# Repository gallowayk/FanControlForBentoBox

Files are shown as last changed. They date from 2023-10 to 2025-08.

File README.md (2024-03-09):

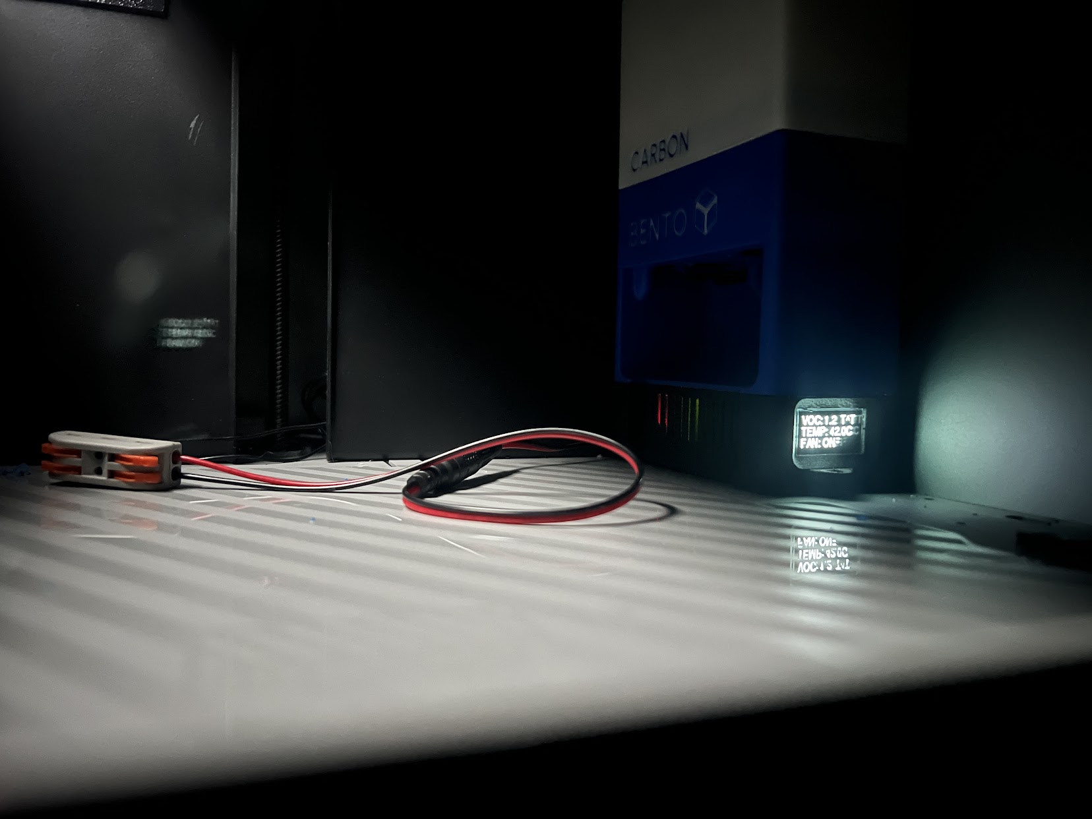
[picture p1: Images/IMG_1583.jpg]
Full Unit in Place


After printing out the Bento Box filtration model, I wanted a means to control the fans so they weren't on 24/7 and only enabled when high VOC content was present. Originally, I was only going to use a bimetal temp switch since the ambient internal temperature of the printer would only rise while printing ABS, PC, Nylon, etc. However, I wanted to take a more sophisticated approach while keeping costs low. 

**Electronics**
- RPi Pico (any variant)
- 3.3V trigger opto-isolated relay https://www.amazon.com/dp/B07XGZSYJV 
- MS1100 gas sensor https://www.amazon.com/dp/B0BF4JDW26
- AHT21 temperature and humidity sensor https://www.amazon.com/HiLetgo-Precision-Temperature-Humidity-2-0-5-5V/dp/B09KGW1G41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
- 128x64px SSD1306 OLED screen https://www.amazon.com/gp/product/B0833PF7ML 
- LM2596S buck converter https://www.amazon.com/gp/product/B07QKHR6PY 
    - The buck converter must be adjusted to +5VDC or +3/3.3VDC

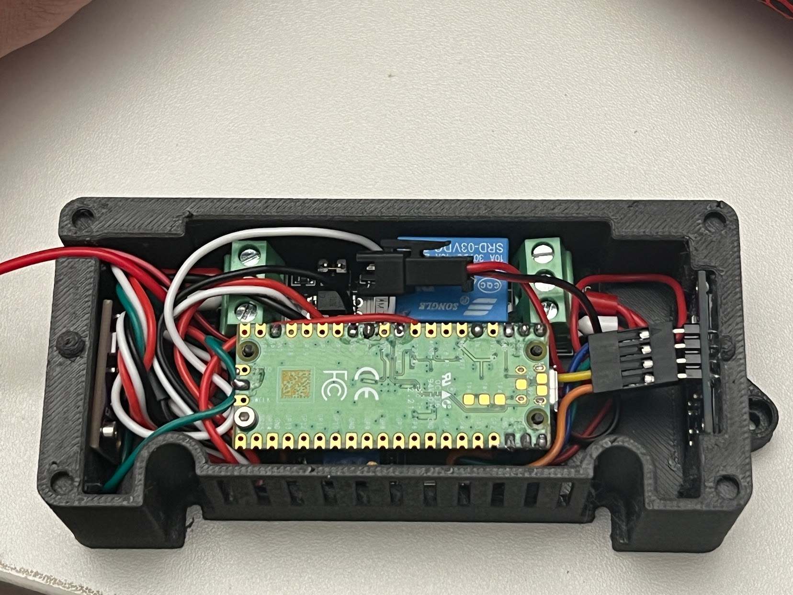
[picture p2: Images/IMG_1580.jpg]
Assembled Electronics box


**Hardware**
- 2x M2x5 or M2x8 self-tapping screw
  - One for VOC sensor
  - One for RPi Pico
- 8x 4x2mm Magnets
- Various jumper wires
- Helps to use male to female jumper wires
- It also helps to have a Dupont connection/terminal kit and crimper; this will allow you to make your own wires of just the right length

**Tools**
- Soldering iron
- TS100 is my go-to due to its rapid heating and cooling
- "Helping hands" for soldering
- Precision tool set
- Ball-end hex keys can be used as well
- Ferrule crimper + ferrules
- Heatshrink

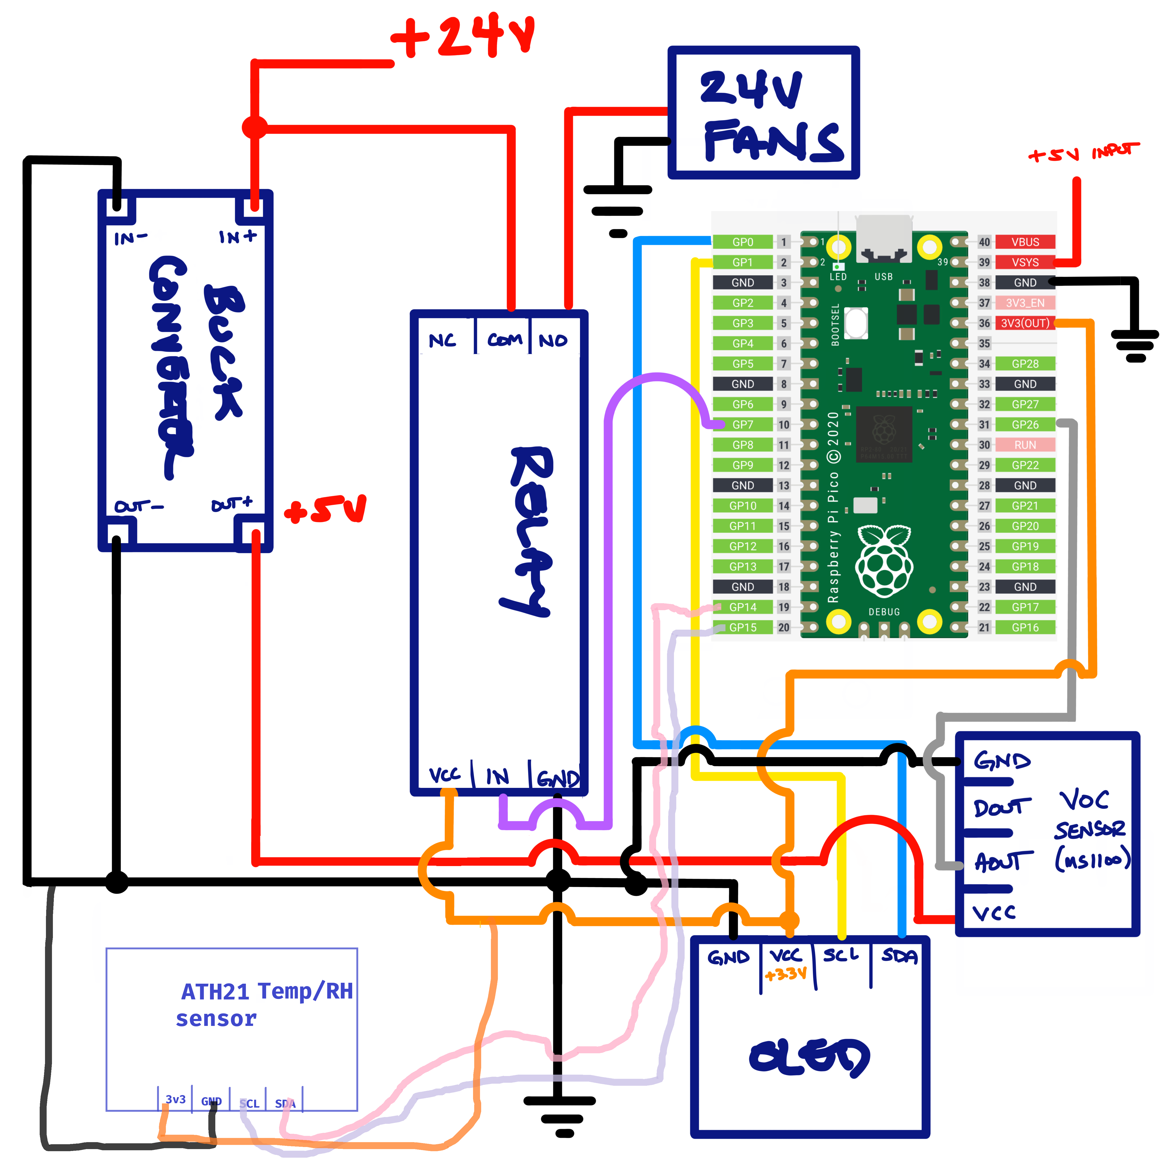
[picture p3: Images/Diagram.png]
Wiring Diagram
 

**Note: Please be sure to safely work on your electronics.**

Do not work on anything while power is connected
Do your best to avoid inhaling the flux/solder fumes

**Software**
Please read through the entire program to acclimate yourself with the functionality!
Pin definitions can be easily changed at the top from those I chose to use.
For those who haven't used Raspberry Pis for their own scripts, save “main.py” to your RPi Pico. When power is applied, this program will run automatically. 

For the program to run you need to also install some packages to the pico board as follow
 - picozero
 - ssd1306 (for the led screen)
 - time
 - typing_extensions
 - micropython_ahtx0 (for the external temp sensor)

 Recomended to use the [Thonny IDE](https://thonny.org/) for package management and connection to the pico

 Before uploading the main.py you need to install the micropython firmware to the pico more details [MicroPython Downloads](https://micropython.org/download/) please select your model from the list.

When I have a bit more time, I'll create a full write up with instructions on how to connect everything. Until then, feel free to ask me questions. Please note, however, that I may not be able to respond quickly.
There are still some tweaks I'd like to make, so a revision may come at some point. I want to reduce the clutter in the electronics housing by utilizing integrated solutions or developing my own PCB with an RP2040 chip and on-board power handling.

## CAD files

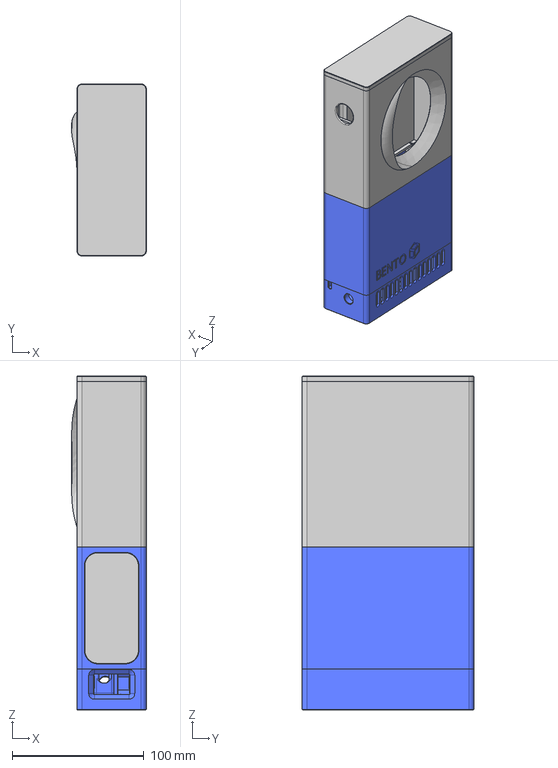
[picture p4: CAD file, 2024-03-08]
CAD/Experimental/Ooki - 120mm Blower Fan Bento.step
56.8 x 130.8 x 254.0 mm

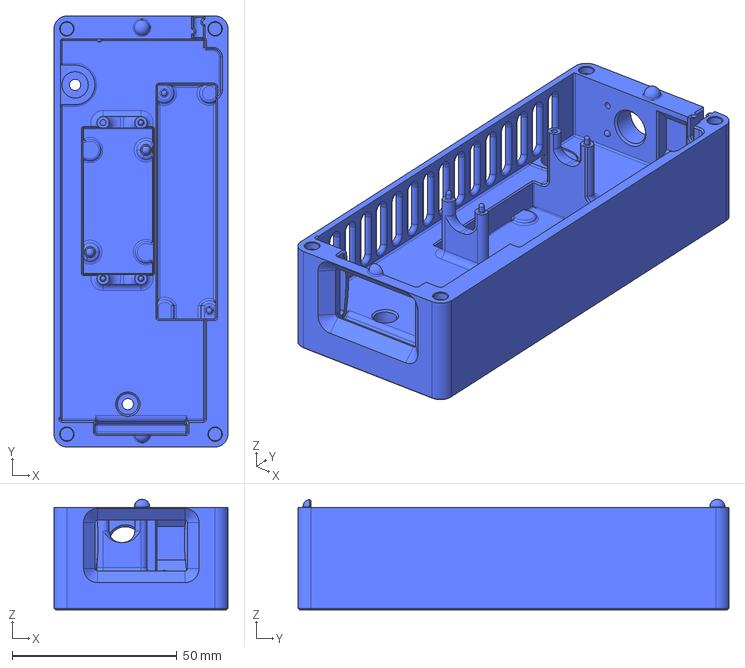
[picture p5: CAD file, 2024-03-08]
CAD/NewElectronicsHousing.step
52.8 x 130.8 x 33.6 mm

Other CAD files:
STLs/ElectronicsHousing.stl
STLs/Cover.stl

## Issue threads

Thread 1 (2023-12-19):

Wiring diagram

benji877, 2023-12-19:
What sort of ETA could I hope for to see a wiring diagram? Anything loosely pointing me in the correct direction would be stellar. Thanks.

gallowayk, 2023-12-21:
Hi Benji, I'll get one drafted over the next few days. Expect it by middle of next week. Thanks!

iruYo, 2024-01-13:
> Hi Benji, I'll get one drafted over the next few days. Expect it by middle of next week. Thanks!

Hey gallowayk! Any news on this? I'd love to try this out

younggulch, 2024-01-17:
I would also love to try this out! Looking forward to the wiring diagram!

gallowayk, 2024-01-17:
Hi all, deepest apologies for the delay. I've been a bit swamped after starting a new job. If you don't want to wait, I would suggest reading through the Python code and reviewing the Rpi Pico pin definitions at the top. I used all common grounds and separated +5V and +24V.

I'm also working on two additional versions of this. One will use a 120mm blower fan and two VOC sensors + the OLED readout. The other will be a lite version that omits the Rpi and OLED, purely running off the calibrated digital output of the VOC sensors.

gallowayk, 2024-03-05:
Wiring diagram included in images. Closing issue.

Closed 2024-03-05.

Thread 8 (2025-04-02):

AHT21 location?

Shy, 2025-04-02:
I'm using your image from printables to figure out the layout.

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

Curious where you would put the AHT21 temperature and humidity sensor? Not seeing it in the picture.

kovacsalexandrurobert, 2025-08-27:
It can be added outside, or at the top of the intake. I did not had the time to do the stl for a container of it.

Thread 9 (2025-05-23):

VOC sensor choice and other things

pkdick, 2025-05-23:
Hello,

I would like to use your system in my Centauri Carbon but I have some questions:

- Why did you choose the MS1100 sensor as it is not designed to detect styren vapors? I found in an Arduino forum that the TPM-300E would be more suited ...
- Moreover, I noticed that you changed you software: as a Linux Noob, I don't know how to use the new version... Could you give me a piece of advice?
- Could it be possible to add the Elegoo logo in your script (I noticed that you designed all printers logo to the exception of Elegoo)?

Thank you for your support!
Best regards

gallowayk, 2025-06-05:
Hi, thanks for your questions!

I went with what I had on-hand and what was what I thought was most cost effective, and honestly... I'm a total noob when it comes to gas/particle sensing. I'm going to look into that sensor and I'll update.

As for the code, there have been other contributors who committed to the main branch. I will clean up the code in the next day or two.

pkdick, 2025-06-05:
Hello,

Thank you for your support!

I printed your design and procured most parts of your list: I am just about
to wire everything and test it.
Please find my link: https://forum.arduino.cc/t/tpm-300e-v2-1/230336

You can also find the sensor in Aliexpress.

By the way if you can add "Elegoo" as a logo for the boot of your software:
as a Linux Noob, I could just download you script and uploaded it to a RPI
picore (I chose a wifi version as I saw that you programmed something).

Best regards

Le 5 juin 2025 05:05:07 gallowayk ***@***.***> a écrit :
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

--1973eb7c1e638b328f3dd858ef
Content-Type: text/html; charset="UTF-8"
Content-Transfer-Encoding: quoted-printable

<!DOCTYPE HTML PUBLIC "-//W3C//DTD HTML 4.01 Transitional//EN" "http://www.=
w3.org/TR/html4/loose.dtd"><html>
<head>
<meta http-equiv=3D"Content-Type" content=3D"text/html; charset=3Dutf-8"></=
head>
<body>
<div dir=3D"auto">
<div dir=3D"auto">Hello,</div><div dir=3D"auto"><br></div><div dir=3D"auto"=
>Thank you for your support!</div><div dir=3D"auto"><br></div><div dir=3D"a=
uto">I printed your design and procured most parts of your list: I am just =
about to wire everything and test it.</div><div dir=3D"auto">Please find my=
 link: <a href=3D"https://forum.arduino.cc/t/tpm-300e-v2-1/230336">https://=
forum.arduino.cc/t/tpm-300e-v2-1/230336</a></div><div dir=3D"auto"><br></di=
v><div dir=3D"auto">You can also find the sensor in Aliexpress.</div><div d=
ir=3D"auto"><br></div><div dir=3D"auto">By the way if you can add &quot;Ele=
goo&quot; as a logo for the boot of your software: as a Linux Noob, I could=
 just download you script and uploaded it to a RPI picore (I chose a wifi v=
ersion as I saw that you programmed something).</div><div dir=3D"auto"><br>=
</div><div dir=3D"auto">Best regards&nbsp;</div>
<div dir=3D"auto"><br></div>
<div dir=3D"auto"><br></div>
<div id=3D"aqm-original" style=3D"color: black;">

<div class=3D"aqm-original-body">
<div style=3D"color: black;">
<p style=3D"color: black; font-size: 10pt; font-family: sans-serif; margin:=
 8pt 0;">Le 5 juin 2025 05:05:07 gallowayk ***@***.***&gt;=
 a =C3=A9crit :</p>
<blockquote type=3D"cite" class=3D"gmail_quote" style=3D"margin: 0 0 0 0.75=
ex; border-left: 1px solid #808080; padding-left: 0.75ex;">
<div style=3D"display: flex; flex-wrap: wrap; white-space: pre-wrap; align-=
items: center; ">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<strong>gallowayk</strong> left a c=
omment <a href=3D"https://github.com/gallowayk/FanControlForBentoBox/issues=
/9#issuecomment-2942594096">(gallowayk/FanControlForBentoBox#9)</a></div>
<p dir=3D"auto">Hi, thanks for your questions!</p>
<p dir=3D"auto">I went with what I had on-hand and what was what I thought =
was most cost effective, and honestly... I'm a total noob when it comes to =
gas/particle sensing. I'm going to look into that sensor and I'll update.</=
p>
<p dir=3D"auto">As for the code, there have been other contributors who com=
mitted to the main branch. I will clean up the code in the next day or two.=
</p>

<p style=3D"font-size:small;-webkit-text-size-adjust:none;color:#666;">=E2=
=80=94<br>Reply to this email directly, <a href=3D"https://github.com/gallo=
wayk/FanControlForBentoBox/issues/9#issuecomment-2942594096">view it on Git=
Hub</a>, or <a href=3D"https://github.com/notifications/unsubscribe-auth/AK=
HHW4LGI4XBZUSMXHT2JY33B6XV5AVCNFSM6AAAAAB5X3ZA4CVHI2DSMVQWIX3LMV43OSLTON2WK=
Q3PNVWWK3TUHMZDSNBSGU4TIMBZGY">unsubscribe</a>.<br>You are receiving this b=
ecause you authored the thread.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<span style=3D"color: transparent; font-size: 0; display: n=
one; visibility: hidden; overflow: hidden; opacity: 0; width: 0; height: 0;=
 max-width: 0; max-height: 0; mso-hide: all">Message ID: <span>&lt;galloway=
k/FanControlForBentoBox/issues/9/2942594096</span><span>@</span><span>githu=
b</span><span>.</span><span>com&gt;</span></span></p>

</blockquote>
</div>
</div>

</div><div dir=3D"auto"><br></div>
</div></body>
</html>

--1973eb7c1e638b328f3dd858ef--

kovacsalexandrurobert, 2025-08-27:
If you need help with the software I can help you with that.

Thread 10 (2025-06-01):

bento box v2 design?

yhs9421877, 2025-06-01:
Can you make a fan box and electronics housing for bento box v2?

Closed 2025-06-01.

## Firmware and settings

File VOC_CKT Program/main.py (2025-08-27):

import json
from machine import Pin, I2C, ADC
from picozero import pico_led
import time
import framebuf
import freesans20
import writer
import ahtx0
import _thread
from web_server import WebServer
import bluetooth
# Remove BLE imports since they're handled in boot.py
# from ble_simple_peripheral import BLESimplePeripheral
import asyncio
from os import uname
from display_service import DisplayService
from Sensors import Sensors

with open("config.json") as f:
    config = json.load(f)
    
connection_state = False
sensors = Sensors(config['sensors'])
display = DisplayService(connection_state, config['display'])

# BLE and InitService are already initialized in boot.py
# No need to create duplicate instances here

# Set the debounce time to 0. Used for switch debouncing
debounce_time=0

# Create a Pin object for the onboard LED, configure it as an output

# Initialize the LED state to 0 (off)
#     led_state = 0

#GPIO Pin Number Definitions; use whatever pin numbers you want
button_pin = 7 #Pin for button
led_pin = 25 #On-board LED = GPIO25; change if using external LED
fan_pin = 22 #GPIO pin of fan relay signal

#set up button (optional)
#button = Pin(button_pin,Pin.IN, Pin.PULL_DOWN)

#LED Setup
led = Pin(led_pin, Pin.OUT)

#set up fan trigger pin
fan_relay = Pin(fan_pin, mode=Pin.OUT)

# Initialize the LED state to 0 (off)
led_state = 0

# Note: BLE communication is now handled by InitService in boot.py
# The on_rx callback and sp.send() calls are no longer needed here

async def main():
    global count, seconds, voc_level_avg, voc_level_sum, voc_def, show_temp, debounce_time, led_state, display, connection_state
    second_thread = _thread.start_new_thread(display.main, (sensors,)) 
    # Create a Bluetooth Low Energy (BLE) object
    webInterface = WebServer(sensors.temperature, pico_led, led_state, connection_state, 'iPhone 13 Pro Max', 'zakarias')
    def serveWrapper(reader, writer):
        return webInterface.serve(reader, writer, led_state)
#     task_connect = asyncio.create_task(webInterface.connect())
    asyncio.create_task(asyncio.start_server(serveWrapper, "0.0.0.0", 80))
    
    count = 0
    voc_level_sum = 0 
    # Main Loop
    while True:
        connection_state = webInterface.isConnected
        display.setConnectionState(connection_state)
        if count <= config['sensors']['voc']['avg_interval']:
            count += 1
            sensors.updateAirQualityIndex(count)
        else:
            count = 1
            
        if sensors.airQualityIndex >= sensors.voc.threshold:
            fan_relay.on() #relay pin high
            print('Fan ON')
        else: 
            print('Fan Off')
            fan_relay.off()
#         if not webInterface.isConnected:  # If not connected to Wi-Fi
#             webInterface.disconnect()       # Disconnect from current Wi-Fi network
#             webInterface.connect()    # Reconnect to Wi-Fi network
#             if led_state != pico_led.value:
#                 led_state = pico_led.value
#                 webInterface.setLedStatus(led_state)

#            webInterface.setTemperature(temp)


#            fan_relay.on() #relay pin high
#             led.value(1)
#             fan_relay.off() #relay pin low
#             led.value(0)
        if (time.ticks_ms() - debounce_time) > 300:
            # The following lines are no longer needed as BLE communication is handled by InitService
            # if sp.is_connected():  # Check if a BLE connection is established
            #     sp.on_write(on_rx)  # Set the callback function for data reception
            #     ledStatus = "On" if led_state == 1 else "Off"
            #     # Create a message string
            #     msg="LED State:"+ledStatus+" TEMP: {}C".format(round(temp,1))+" %RH: {}%\r\n".format(round(humidity,2))
            #     # Send the message via BLE
            #     sp.send(msg)
            # Update the debounce time    
            debounce_time=time.ticks_ms()

        await asyncio.sleep(0.1)

try:
    asyncio.run(main())  # Run the main asynchronous function
except Exception as e:
    print(f"Error in main: {e}")
finally:
    asyncio.new_event_loop() #Create a new event loop

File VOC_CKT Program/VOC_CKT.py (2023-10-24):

from machine import Pin, I2C, SoftI2C, ADC
from ssd1306 import SSD1306_I2C
import ssd1306
import time
import framebuf
import freesans20
import writer

#GPIO Pin Number Definitions; use whatever pin numbers you want
button_pin = 7 #Pin for button
led_pin = 25 #On-board LED = GPIO25; change if using external LED
voc_sense_pin = 26 #ADC GPIO pin number for VOC sensor
voc_threshold = 1.1 #Threshold to activate system
fan_pin = 22 #GPIO pin of fan relay signal

#set up button (optional)
#button = Pin(button_pin,Pin.IN, Pin.PULL_DOWN)

#LED Setup
led = Pin(led_pin, Pin.OUT)

#set up OLED
i2c=I2C(0,sda=Pin(0), scl=Pin(1), freq=400000)
oled_width = 128
oled_height = 64
oled = SSD1306_I2C(oled_width, oled_height, i2c)

#set up VOC sensor
voc_def = ADC(voc_sense_pin)
voc_conv = 5/65535

#set up fan trigger pin
fan_relay = Pin(fan_pin, mode=Pin.OUT)

count = 0
voc_level_avg = 0
voc_level_sum = 0

bigText = writer.Writer(oled, freesans20)

#bootup splash screen
splash = bytearray(b'\xff\xff\xff\xff\xff\xff\xff\xff\xff\xff\xff\xff\xff\xff\xff\xff\xff\xff\xff\xff\xff\xff\xff\xff\xff\xff\xff\xff\xff\xff\xff\xff\xff\xff\xff\xff\xff\xff\xff\xff\xff\xff\xff\xff\xff\xff\xff\xff\xff\xff\xff\xff\xff\xff\xff\xff\xff\xff\xff\xff\xff\xff\xff\xff\xff\xff\xff\xff\xff\xff\xff\xff\xff\xff\xff\xff\xff\xff\xff\xff\xff\xff\xff\xff\xff\xff\xff\xfe\x7f\xff\xff\xff\xff\xff\xff\xff\xff\xff\xff\xff\xff\xff\xff\xf8\x1f\xff\xff\xff\xff\xff\xff\xff\xff\xff\xff\xff\xff\xff\xff\xf0\x0f\xff\xff\xff\xff\xff\xff\xff\xff\xff\xff\xff\xff\xff\xff\xc0\x03\xff\xff\xff\xff\xff\xff\xff\xff\xff\xff\xff\xff\xff\xff\x00\x00\xff\xff\xff\xff\xff\xff\xff\xff\xff\xff\xff\xff\xff\xfc\x00\x00?\xff\xff\xff\xff\xff\xff\xff\xff\xff\xff\xff\xff\xf0\x01\x80\x0f\xff\xff\xff\xff\xff\xff\xff\xff\xff\xff\xff\xff\xe0\x03\xc0\x07\xff\xff\xff\xff\xff\xff\xff\xff\xff\xff\xff\xff\x80\x0f\xf0\x01\xff\xff\xff\xff\xff\xff\xff\xff\xff\xff\xff\xfe\x00?\xfc\x00\x7f\xff\xff\xff\xff\xff\xff\xff\xff\xff\xff\xf8\x00\xff\xff\x00\x1f\xff\xff\xff\xff\xff\xff\xff\xff\xff\xff\xf0\x03\xff\xff\xc0\x0f\xff\xff\xff\xff\xff\xff\xff\xff\xff\xff\xc0\x07\xff\xff\xe0\x03\xff\xff\xff\xff\xff\xff\xff\xff\xff\xff\x80?\xff\xff\xfc\x01\xff\xff\xff\xff\xff\xff\xff\xff\xff\xff\x00\x7f\xff\xff\xfe\x00\xff\xff\xff\xff\xff\xff\xff\xff\xff\xff\x00\x7f\xff\xff\xfe\x00\xff\xff\xff\xff\xff\xff\xff\xff\xff\xff\x00?\xff\xff\xfc\x00\xff\xff\xff\xff\xff\xff\xff\xff\xff\xff\x00\x0f\xff\xff\xf0\x00\xff\xff\xff\xff\xff\xff\xff\xff\xff\xff\x00\x01\xff\xff\x80\x00\xff\xff\xff\xff\xff\xff\xff\xff\xff\xff\x00\x00\xff\xff\x00\x00\xff\xff\xff\xff\xff\xff\xff\xff\xff\xff\x02\x00?\xfc\x00@\xff\xff\xff\xff\xff\xff\xff\xff\xff\xff\x03\x80\x1f\xf8\x01\xc0\xff\xff\xff\xff\xff\xff\xff\xff\xff\xff\x03\xe0\x03\xc0\x07\xc0\xff\xff\xff\xff\xff\xff\xff\xff\xff\xff\x03\xf8\x00\x00\x1f\xc0\xff\xff\xff\xff\xff\xff\xff\xff\xff\xff\x03\xfc\x00\x00?\xc0\xff\xff\xff\xff\xff\xff\xff\xff\xff\xff\x03\xff\x00\x00\xff\xc0\xff\xff\xff\xff\xff\xff\xff\xff\xff\xff\x03\xff\xc0\x03\xff\xc0\xff\xff\xff\xff\xff\xff\xff\xff\xff\xff\x03\xff\xf0\x0f\xff\xc0\xff\xff\xff\xff\xff\xff\xff\xff\xff\xff\x03\xff\xf8\x1f\xff\xc0\xff\xff\xff\xff\xff\xff\xff\xff\xff\xff\x03\xff\xf8\x1f\xff\xc0\xff\xff\xff\xff\xff\xff\xff\xff\xff\xff\x03\xff\xf8\x1f\xff\xc0\xff\xff\xff\xff\xff\xff\xff\xff\xff\xff\x03\xff\xf8\x1f\xff\xc0\xff\xff\xff\xff\xff\xff\xff\xff\xff\xff\x03\xff\xf8\x1f\xff\xc0\xff\xff\xff\xff\xff\xff\xff\xff\xff\xff\x03\xff\xf8\x1f\xff\xc0\xff\xff\xff\xff\xff\xff\xff\xff\xff\xff\x03\xff\xf8\x1f\xff\xc0\xff\xff\xff\xff\xff\xff\xff\xff\xff\xff\x03\xff\xf8\x1f\xff\xc0\xff\xff\xff\xff\xff\xff\xff\xff\xff\xff\x03\xff\xf8\x1f\xff\xc0\xff\xff\xff\xff\xff\xff\xff\xff\xff\xff\x03\xff\xf8\x1f\xff\xc0\xff\xff\xff\xff\xff\xff\xff\xff\xff\xff\x01\xff\xf8\x1f\xff\x80\xff\xff\xff\xff\xff\xff\xff\xff\xff\xff\x00\x7f\xf8\x1f\xfe\x00\xff\xff\xff\xff\xff\xff\xff\xff\xff\xff\x80?\xf8\x1f\xfc\x01\xff\xff\xff\xff\xff\xff\xff\xff\xff\xff\xc0\x07\xf8\x1f\xe0\x03\xff\xff\xff\xff\xff\xff\xff\xff\xff\xff\xf0\x03\xf8\x1f\xc0\x0f\xff\xff\xff\xff\xff\xff\xff\xff\xff\xff\xf8\x00\xf8\x1f\x00\x1f\xff\xff\xff\xff\xff\xff\xff\xff\xff\xff\xfe\x008\x1c\x00\x7f\xff\xff\xff\xff\xff\xff\xff\xff\xff\xff\xff\x80\x08\x10\x01\xff\xff\xff\xff\xff\xff\xff\xff\xff\xff\xff\xff\xe0\x00\x00\x07\xff\xff\xff\xff\xff\xff\xff\xff\xff\xff\xff\xff\xf0\x00\x00\x0f\xff\xff\xff\xff\xff\xff\xff\xff\xff\xff\xff\xff\xfc\x00\x00?\xff\xff\xff\xff\xff\xff\xff\xff\xff\xff\xff\xff\xff\x00\x00\xff\xff\xff\xff\xff\xff\xff\xff\xff\xff\xff\xff\xff\xff\xc0\x03\xff\xff\xff\xff\xff\xff\xff\xff\xff\xff\xff\xff\xff\xff\xf0\x0f\xff\xff\xff\xff\xff\xff\xff\xff\xff\xff\xff\xff\xff\xff\xf8\x1f\xff\xff\xff\xff\xff\xff\xff\xff\xff\xff\xff\xff\xff\xff\xfe\x7f\xff\xff\xff\xff\xff\xff\xff\xff\xff\xff\xff\xff\xff\xff\xff\xff\xff\xff\xff\xff\xff\xff\xff\xff\xff\xff\xff\xff\xff\xff\xff\xff\xff\xff\xff\xff\xff\xff\xff\xff\xff\xff\xff\xff\xff\xff\xff\xff\xff\xff\xff\xff\xff\xff\xff\xff\xff\xff\xff\xff\xff\xff\xff\xff\xff\xff\xff\xff\xff\xff\xff\xff\xff\xff\xff\xff\xff\xff\xff\xff\xff\xff\xff\xff\xff\xff\xff')
frame = framebuf.FrameBuffer(splash,128,64, framebuf.MONO_HLSB)
oled.invert(1)
oled.fill(0)
oled.blit(frame,0,0)
oled.show()
time.sleep(5)
oled.fill(0)
oled.show()
oled.invert(0)

# Main Loop
while True:
###################### VOC SENSING ########################  
    if count <= 49:
        count += 1
        voc_level_new = voc_def.read_u16() * voc_conv
        voc_level_sum += voc_level_new
        voc_level_avg = voc_level_sum/count
        bigText = writer.Writer(oled, freesans20)
        bigText.set_textpos(0,0)
        if voc_level_avg > 1:
            bigText.printstring("VOC: {}  T^T".format(round(voc_level_avg,1)))
            oled.show()
        else:
            bigText.printstring("VOC: {}  ^_^".format(round(voc_level_avg,1)))
            oled.show()
###################### TEMPERATURE ########################
        temp = ADC(4)
        adc_voltage = temp.read_u16() * 3.3 / 65535
        cpu_temp = 27 - (adc_voltage - 0.706)/0.001721
        bigText.set_textpos(0,21)
        bigText.printstring("TEMP: {}C".format(round(cpu_temp,1)))
        oled.show()
        time.sleep(1)
    else:
        count = 1  #reset counter
        voc_level_sum = voc_level_avg #reset running sum of VOC readings
        oled.fill(0) #clear screen of any artifacts
        oled.show()

##################### RELAY CONTROL ######################
    if voc_level_avg >= voc_threshold:
        fan_relay.on() #relay pin high
        bigText.set_textpos(0,42)
        bigText.printstring("FAN: ON")
        led.value(1)
    else:
        fan_relay.off() #relay pin low
        bigText.set_textpos(0,42) 
        bigText.printstring("FAN: OFF")
        led.value(0)
        

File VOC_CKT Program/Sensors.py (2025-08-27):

import ahtx0
from machine import Pin, I2C, ADC

class Sensors():
    def __init__(self, config):
        print('Sensor config: ', config)

        for key, value in config.items():
#       	This will map config dict to Sensor class properties            
            obj = type('Obj', (object,), {k: v for k, v in value.items()})()
            setattr(self, key, obj )
            
            currentSensor = getattr(self, key)
            
            if currentSensor.analog == True:
                setattr(currentSensor, 'analog_def', ADC(currentSensor.sense_pin))
            else:
                setattr(currentSensor, 'I2C', I2C(currentSensor.I2Channel, sda=Pin(currentSensor.sda_pin), scl=Pin(currentSensor.scl_pin), freq=currentSensor.freq))
        self.voc_level_sum = 0
        self.initAhtxSensor()
        self.initVocSensor()
        
        
    def initAhtxSensor(self):
        self.ahtx.sensor = ahtx0.AHT20(self.ahtx.I2C)
        self._temperature = self.ahtx.sensor.temperature
        self._humidity = self.ahtx.sensor.relative_humidity
    
    def initVocSensor(self):
        #           Special case for our VOC sensor used, it is for calibration.
        voc_conv = 5/65535
        setattr(self.voc, 'conversion', voc_conv)
        setattr(self.voc, 'voc_level_avg', 0)
    
    @property
    def temperature(self):
        return self.ahtx.sensor.temperature
    
    @property
    def humidity(self):
        return self.ahtx.sensor.relative_humidity
    
    def updateAirQualityIndex(self, interval):
        currentValue = self.voc.analog_def.read_u16() * self.voc.conversion
        self.voc_level_sum += currentValue
        if interval <= self.voc.avg_interval:
            self.voc_level_avg = self.voc_level_sum/interval
        else:
            self.voc_level_sum = self.voc_level_avg

    @property
    def airQualityIndex(self):
        return self.voc_level_avg
        

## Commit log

2023-10-24 Add files
    Added:
    - STLs
    - One more image
    Created directories:
    - STLs
    - Images
    [Cover.stl]
2023-10-24 Readding
    Using LFS
    [Cover.stl, ElectronicsHousing.stl]
2024-01-27 Wiring Diagram
    As always, please double check all wiring before energizing. All DIY work is done at one's own and property's risk.
2024-03-05 feature: added temp sensor and different splash screens
2024-03-05 chore: removed print from code
2024-03-08 Add CAD + Experimental "Ooki" CAD
    "Ooki" is a 120mm blower fan bento with a modified filter and fan housing. The idea is better static pressure for more effective filtration.
    [NewElectronicsHousing.step, Ooki - 120mm Blower Fan Bento.step]
2024-03-13 corrected connection timings and initialization for pico w
    [main.py]
2024-03-13 refactored to detect board and split to services: ex display service webservice bluetoothservice
2024-05-01 split up services and added sensor modules
2025-08-27 feat: Implement BLE device binding and user configuration
    [InitService.py, boot.py]
2025-08-27 feat: Implement SmartBento device naming and BLE reset functionality
    - Add custom device name generation (SmartBento-4charUUID)
    - Implement BLE hard reset with cleanup before advertising
    - Fix InitService integration and device setup flow
    - Add Ctrl+C interrupt handling in boot.py
    - Clean up duplicate BLE files and imports
    - Update device advertising to use SmartBento naming convention
    [InitService.py, ble_advertising.py, ble_simple_peripheral.py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]
